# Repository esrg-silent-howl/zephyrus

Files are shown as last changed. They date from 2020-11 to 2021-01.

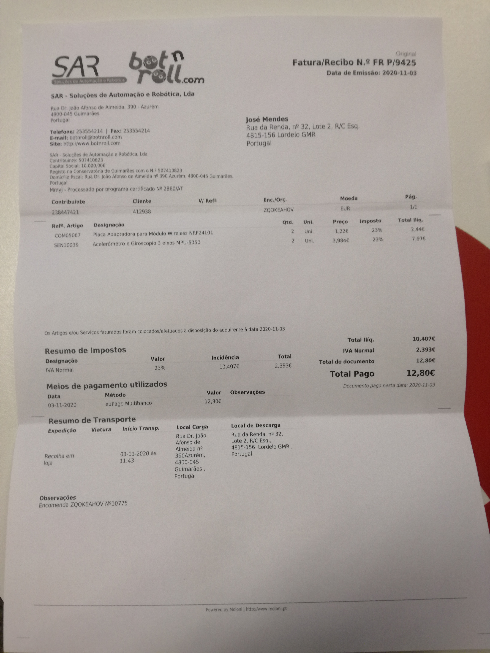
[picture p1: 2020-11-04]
Documents/Material/media/2020_11_03.jpg

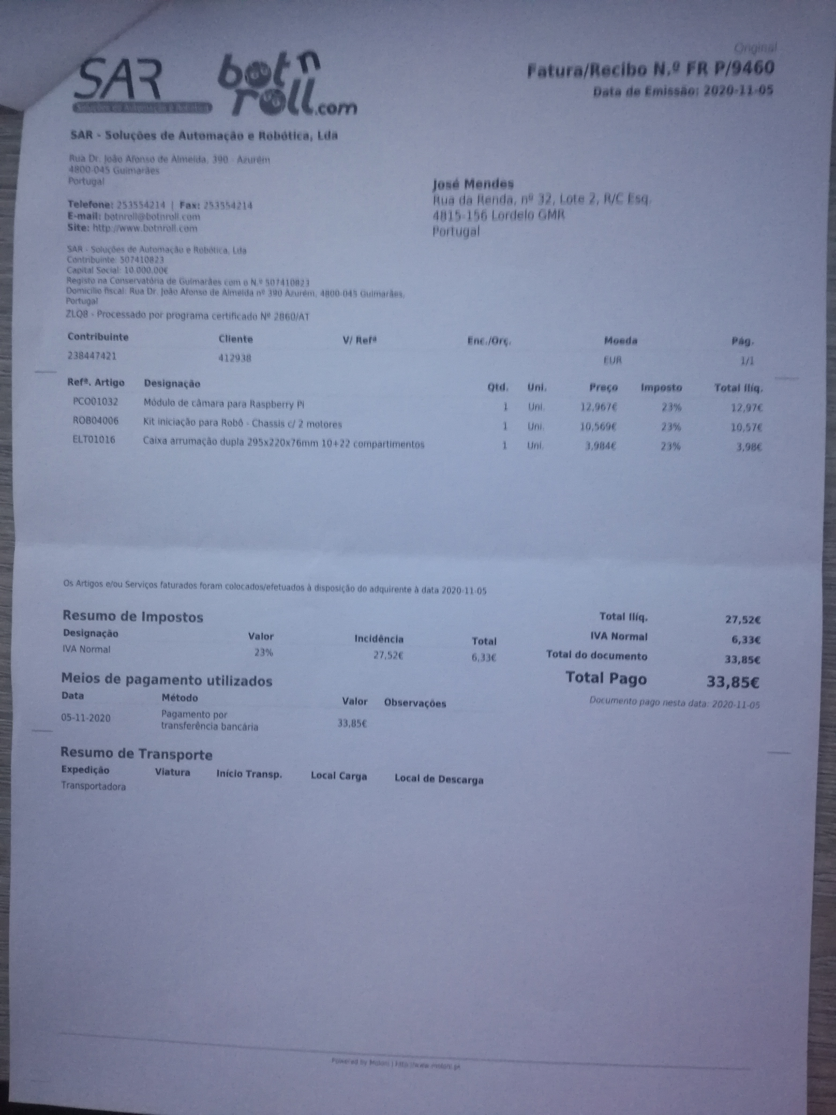
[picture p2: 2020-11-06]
Documents/Material/media/2020_11_05.jpg

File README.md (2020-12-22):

# Zephyrus
## Hand Motion-Controlled Remote Car

### Problem Statement
Recent developments in research of motion-tracking and gesture-controlled robotic
products have shone a new light on entertainment, special needs teaching, and
accessibility-focused applications. Products like motion-sensing console controllers,
robotic arms, and prosthetics have popularized and extended the knowledge on gesture
and impulse-based technologies throughout the past few years, and their market
is predicted to continue to grow in the future.
To provide a better understanding of the concepts associated with the forementioned
technologies through Research and Development (R&D), the project will consist of a
gesture-controlled car with a wristband as a remote controller. The user will be able to
accelerate and steer the vehicle using natural wrist and finger movements.

Team:
- Hugo Carvalho @HugoDaniel99
- José Mendes @h0wl-14

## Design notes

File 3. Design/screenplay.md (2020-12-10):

### **1.Introduction**

Good afternoon. We are group 7 and we are going to present the design for project 1. Its name is Zephyrus and its intent is to implement a wrist motion-controlled remote car.

### **2. Agenda**

Here is the agenda for the presentation.

- Problem Statement  
- System Overview
- Hardware and Software Architectures
- Hardware Specification
- Peripheral Interface
- Software Specification
  - Local System
  - Reinforcement Learning
  - Remote System
- Test Cases
  - Local System
  - Remote System
  - Integration
- Gantt Diagram  

### **3. Problem statement**

Motion-tracking and gesture-controlled robotics have been gaining popularity in various professional areas.  

With that in mind, this project intends to serve as a research and development tool for wearable-controlled technologies and will consist of a car, remotely controlled by a wristband using natural wrist and finger movements.  

### **4, 5, 6. System Overview**

This Figure depicts the system overview, where one can identify the main and remote boards and the ways in which they interact with each other and the external environment.

### **7. Hardware Architecture**

The Hardware for the  Local System includes: 

- A more capable main controller;
- Sensors for measuring proximity to close objects and positioning in the horizontal plane;
- Actuators for motor control ;
- A short-range wireless communications device;
- A power supply unit.

The Hardware for the Remote System includes: 

- An energy-efficient main controller;
- Sensors for measuring hand positioning;
- The counterpart for the short-range wireless communications device in the local system;
- A power supply unit.

### **8. Software Architecture**

The software architecture for both devices include high abstraction for communicating with each other and sensing modules, as well as power management and task scheduling. The local system, specifically, includes two high-level layers of abstraction for the Reinforcement Learning model.  

### **9. Hardware Specification: Local (Logic Elements)**

The main functional roles of the Local System are played by:

- A NUCLEO-F767ZI board, which hosts the main controller and all the components used to program it and make it work;
- A module containing an accelerometer/gyroscope IC that can be controlled through an I2C interface;
- A module containing a short-range radio IC and antenna instrumentation, for wireless communication;
- An board which contains an ultrasonic sensor and respective instrumentation;
- A very simple voltage level converter board to serve as **glue logic** between the main controller and the ultrasonic sensor board;
- A module containing a dual-motor driver IC.

### **10. Hardware Specification: Local (Power Supply)**

The elements that make up the power supply unit for the Local System are:

- A pair of Li-Ion batteries;
- A Battery Management System board;
- A 5V switching DC-DC step-down converter board.

### **11. Hardware Specification: Remote**

The hardware on the Remote System is comprised mainly by:

- An accelerometer and gyroscope module like the one on the Local System;
- An RF communication module that matches the one on the Local System;
- An exchangeable coin cell that serves as the main power supply for the system;
- A push button ON/OFF controller IC.

### **12. Hardware Specification: Custom Hardware (Prototype Alpha) SCH**

In order to develop for the remote system's microcontroller, a simple board was devised. This solution contains the minimum components and interfaces to be used by any microcontroller in the STM32F0 family of devices (with a QFP32 package). Additionally, it is simple enough to provide accurate real-world power profiling, necessary for alpha testing low-power applications, which is the case in this project.

The schematic for this board, designed in EAGLE CAD is represented in this image.

### **13. Hardware Specification: Custom Hardware (Prototype Alpha) BRD**

Here one can see the blueprints for that same board, with its dimensions and a glimpse of the outcome.

### **14. Hardware Specification: Custom Hardware (Prototype Beta) UC**

Following the alpha prototype, it was decided that there would be a beta prototype, containing all the integrated solutions that make up the wristband, into a slim and portable format.

With the aid of STM32CubeMX, one was able to plan out the pinout configuration and labelling for the Remote System's MCU.

### **15, 16. Hardware Specification: Custom Hardware (Prototype Beta) SCH**

Here are the initial schematics for the final wristband prototype, considering the predefined labels and separated by function into Main Logic and Power and Radio.  

### **17. Peripheral Interface: Common**

Here are the schematics documenting the interfaces between the microcontroller and the rest of the hardware. This one is for the hardware that is common to both systems...

### **18. Peripheral Interface: Specific**

... and this one is for hardware that is specific to one of the two.

### **19. Software Specification: Task Priority**

The thread pool for each system is represented in these diagrams, along with their relative priorities, statically defined. 

### **20. Software Specification: Task Timelines**

To ensure the meeting of critical timing constraints, a priority-based scheduling scheme with preemption was devised for each system. For both of them, one considered each task's worst case scenario in terms of processor time usage, as well as the power/efficiency trade-off. Dead time between task execution will be used to put the system asleep, favouring low power consumption.

### **21. Software Specification: Task Communication**

This is a diagram describing the means by which the tasks in each system interact with each other. These mechanisms satisfy what was laid out in the task timelines referring to inter-thread communication and synchronism.

### **22, 23, 24, 25. Software Specification: Threads**

As every other aspect of the project, the tasks' workflows also need a design stage. Here we can see the flowcharts for the most complex ones:

- The Local System's:
  - Gyroscope and accelerometer management task
  - RF communications management task
  - The inference task
- The Remote System's:
  - Gyroscope and accelerometer management task
  - RF communications management task

### **26. System Overview (Reinforcement Learning)**

The Local System will have a Reinforcement Learning module that is highlighted in this system overview.

### **27. System Overview (Reinforcement Learning)**

Zephyrus will rely on a feed-forward neural network that takes as input percentage speed and steer reference values, front and back measurements of distance to the nearest obstacle, and the environment state provided by the on-board sensors. With that in mind, the network will output the average percentage of the maximum voltage to be output to the motors. Percentage values were used to allow for portability to loads that require different working voltages.

### **28, 29. Test Cases**

At this stage, it is important to define a test strategy. Considering this, the tests were split into unit and integration tests taking into account alpha and beta prototypes.

### **30. Gantt Diagram**

The Gantt Diagram is presented in this slide and presents the tasks assigned to each week until the deadline.

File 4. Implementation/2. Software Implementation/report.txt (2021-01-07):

- microcontroller will shut the system off in 2 different situations:
	- user request, peacefully
	- undetermined hard fault

- check memory footprint

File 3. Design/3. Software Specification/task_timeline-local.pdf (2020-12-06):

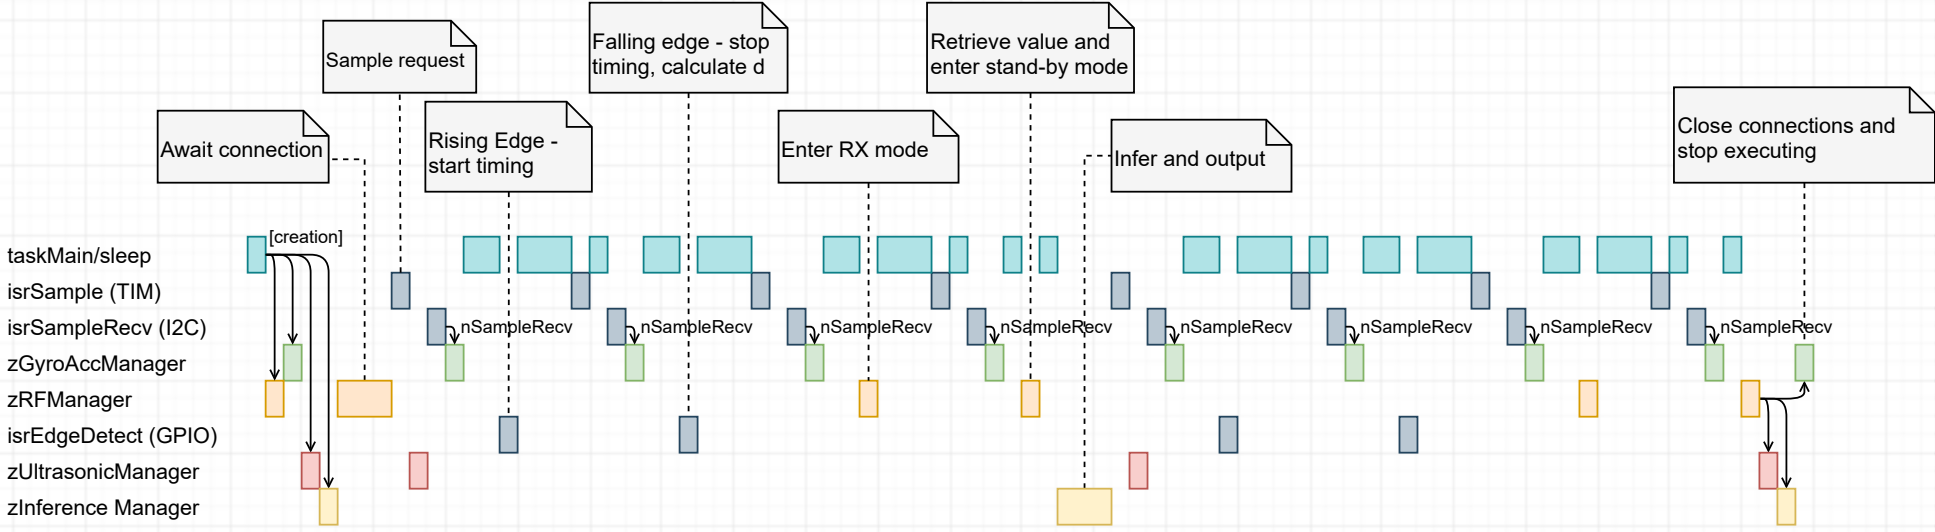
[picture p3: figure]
taskMain/sleep; isrSample (TIM); zGyroAccManager; isrSampleRecv (I2C); nSampleRecv; zRFManager; Sample request; Close connections and stop executing; [creation]; zUltrasonicManager; Enter RX mode; Retrieve value and enter stand-by mode; isrEdgeDetect (GPIO); Rising Edge - start timing; zInference Manager; Await connection; Falling edge - stop timing, calculate d; Infer and output

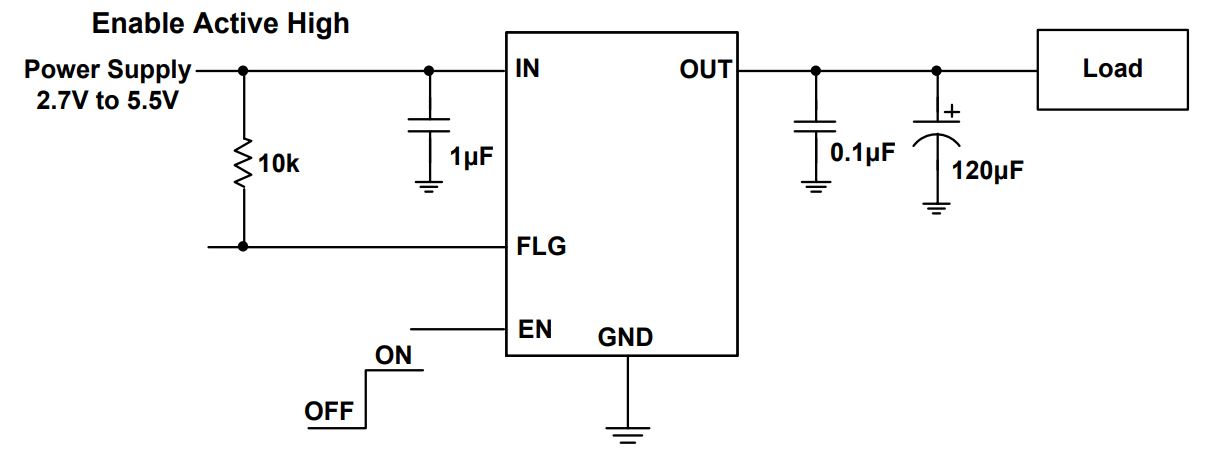
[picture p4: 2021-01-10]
3. Design/1. Hardware Specification/media/application_diagrams/ap22814.JPG

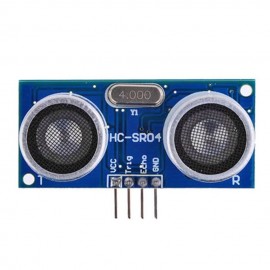
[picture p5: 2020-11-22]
3. Design/1. Hardware Specification/media/hc-sr04.jpg

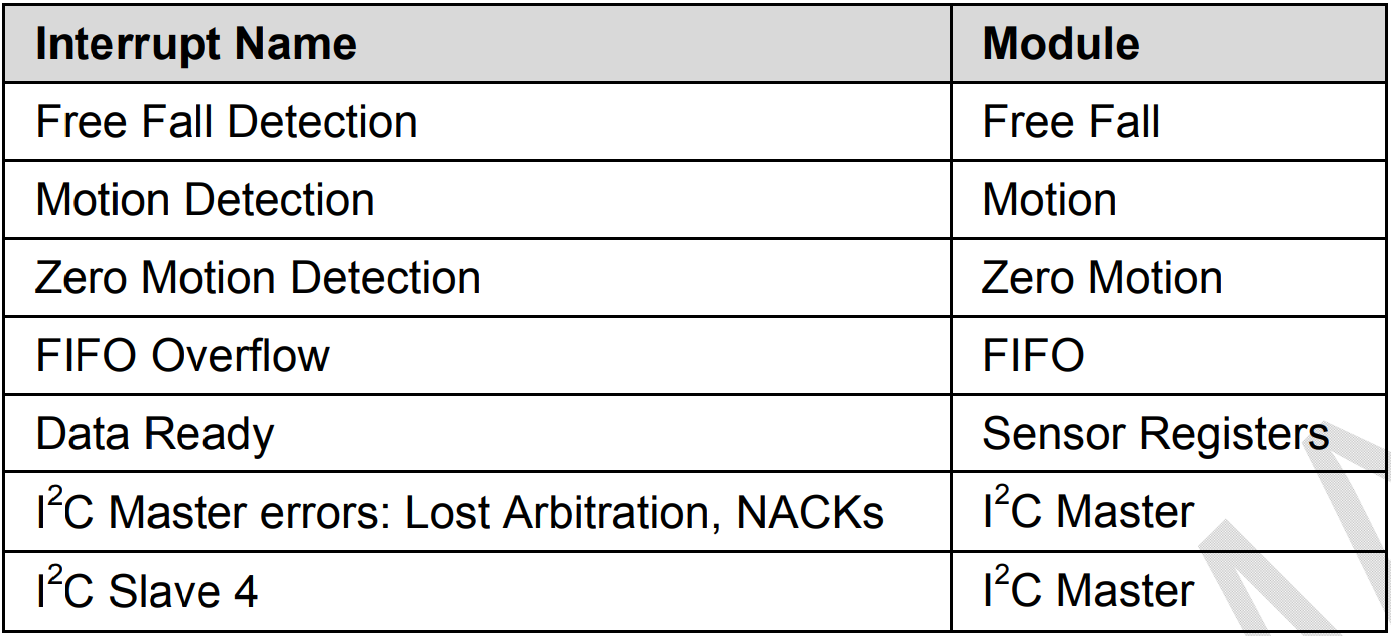
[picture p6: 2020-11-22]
3. Design/3. Software Specification/media/mpu-6050-interrupt-table.png

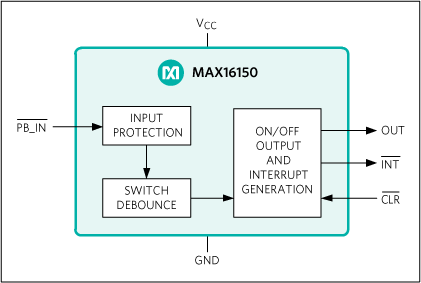
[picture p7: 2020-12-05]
3. Design/2. Interfaces/1. Peripherals/media/max16150-pinout.png

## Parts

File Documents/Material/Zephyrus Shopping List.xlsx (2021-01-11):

Date | Product Description | Quantity | Total | Store | Shipping & Customs | Element
2020-11-03 | nRF24L01+ module adapter | 2 | 3 | bot'n'roll | 0 | -
 | MPU-6050 (acc./gyro) | 2 | 9.8
2020-11-05 | Robot platform | 1 | 13 | bot'n'roll | 0 | -
2020-11-23 | STM32F051 dev board PCB | 1 | 2.11 | JLCPCB | 14.15 | -
2020-12-03 | last integrated modules | - | 32.75 | bot'n'roll | 0 | -
2020-12-22 | Wristband & PB ON/OFF PCB | - | 6.54 | JLCPCB | 12.09 | -
2020-12-22 | Components for final prototypes | - | 66.75 | Mouser | 0 | -
2020-12-29 | nRF24L01+ and nRF24L01+ module adapter | 2 | 10 | bot'n'roll | 0 | -

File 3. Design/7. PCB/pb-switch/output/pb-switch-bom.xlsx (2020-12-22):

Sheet: Sheet1
Exported
Qty | Value | Device | Package | Parts | Description | Column1 | _1
1 |  | CONN_06SILK_FEMALE_PTH | 1X06 | J2 | Multi connection point. Often used as Generic Header-pin footprint for 0.1 inch spaced/style header connections
3 | 1.4K[0603] | R-US_CHIP-0603(1608-METRIC) | RESC1608X60 | R1, R5, R6 | Resistor Fixed - ANSI
2 | 100n [0603] | C_CHIP-0603(1608-METRIC) | CAPC1608X85 | C1, C2 | Capacitor - Generic
1 | AP22814AW5-7 | AP22814AW5-7 | SOT95P285X130-5N | PS1 | DiodesZetex AP22814AW5-7, USB Power Switch, High Side, 65m, 1.6 V min. 5-Pin, SOT25
1 | B3F-1000 | B3F-1000 | B3F-1000 | SW1 | Tactile Switch SPST-NO Top Actuated Through Hole
1 | MAX16150AUT+T | MAX16150AUT+T | SOT95P280X145-6N | PB_CTRL | Supervisory Circuits Nano-Power Pushbutton ON/OFF Controller with 15kV ESD Protection and Programmable Timer
Final
Qty | Value | Device | Package | Parts | Description | Column1 | _1
3 | 1.5 KOhm | Resistor | RES0603 | R1, R5, R6 | Resistor Fixed - ANSI
2 | 100 nF | Capacitor | CAP0603 | C1, C2 | Capacitor - Generic
1 | - | AP22814AW5-7 | SOT23-5 | PS1 | High Side Power Switch
1 | - | MAX16150AUT+T | SOT23-6 | PB_CTRL | Pushbutton ON/OFF Controller

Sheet: pb_switch_bom
Qty;"Value";"Device";"Package";"Parts";"Description";"";
1;"";"CONN_06SILK_FEMALE_PTH";"1X06";"J2";"Multi connection point. Often used as Generic Header-pin footprint for 0.1 inch spaced/style header connections";"";
3;"1.4K[0603]";"R-US_CHIP-0603(1608-METRIC)";"RESC1608X60";"R1 | R5 | R6";"Resistor Fixed - ANSI";"";
2;"100n [0603]";"C_CHIP-0603(1608-METRIC)";"CAPC1608X85";"C1 | C2";"Capacitor - Generic";"";
1;"AP22814AW5-7";"AP22814AW5-7";"SOT95P285X130-5N";"PS1";"DiodesZetex AP22814AW5-7 | USB Power Switch | High Side | 65m | 1.6 V min. 5-Pin | SOT25";"";
1;"B3F-1000";"B3F-1000";"B3F-1000";"SW1";"Tactile Switch SPST-NO Top Actuated Through Hole";"";
1;"MAX16150AUT+T";"MAX16150AUT+T";"SOT95P280X145-6N";"PB_CTRL";"Supervisory Circuits Nano-Power Pushbutton ON/OFF Controller with 15kV ESD Protection and Programmable Timer";"";

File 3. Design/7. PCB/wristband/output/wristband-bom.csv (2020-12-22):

Qty | Value | Device | Package | Parts | Description | Column1 | _1
3 | 1.4K[0603] | R-US_CHIP-0603(1608-METRIC) | RESC1608X60 | R1, R5, R6 | Resistor Fixed - ANSI
2 | 1.5k [0603] | R-US_CHIP-0603(1608-METRIC) | RESC1608X60 | R3, R8 | Resistor Fixed - ANSI
2 | 100n [0603] | C_CHIP-0603(1608-METRIC) | CAPC1608X85 | C1, C2 | Capacitor - Generic
1 | 10K[0603] | R-US_CHIP-0603(1608-METRIC) | RESC1608X60 | R7 | Resistor Fixed - ANSI
5 | 10nF [0603] | CAPACITOR_0603_L | RESC0603_L | C5, C7, C21, C22, C24 | Generic chip capacitor
2 | 1nF [0603] | CAPACITOR_0603_L | RESC0603_L | C4, C6 | Generic chip capacitor
1 | 1uF [0603] | CAPACITOR_0603_L | RESC0603_L | C23 | Generic chip capacitor
1 | 2.2 nF [0603] | CAPACITOR_0603_L | RESC0603_L | C8 | Generic chip capacitor
1 | 22K[0603] | R-US_CHIP-0603(1608-METRIC) | RESC1608X60 | R2 | Resistor Fixed - ANSI
5 | 22nF [1206] | CL31B226KPHNNNE | CAPC3216X180N | C10, C11, C12, C13, C14 | 22F +/-10% 10V Ceramic Capacitor X7R 1206 (3216 Metric)
4 | 22pF [0603] | CAPACITOR_0603_L | RESC0603_L | C15, C16, C17, C18 | Generic chip capacitor
1 | 2450BM14A0002T | 2450BM14A0002T | 2450BM14A0002T | ANT1 | JOHANSON TECHNOLOGY - 2450BM14A0002T - BALUN, 2.45GHZ, IMPEDANCE MATCHED
1 | 33nF [0603] | CAPACITOR_0603_L | RESC0603_L | C3 | Generic chip capacitor
2 | 4.7uF [0603] | CAPACITOR_0603_L | RESC0603_L | C19, C20 | Generic chip capacitor
1 | AP22814AW5-7 | AP22814AW5-7 | SOT95P285X130-5N | PS2 | DiodesZetex AP22814AW5-7, USB Power Switch, High Side, 65m, 1.6 V min. 5-Pin, SOT25
1 | BAT-HLD-001 | BAT-HLD-001 | BATHLD001 | BATT_HLD | Coin Cell Battery Holders Linx CR2032 Battery Holder
1 | DELLS1.22-AMBER | KS_DELLS1.22-JHKI-1 | KSDELLS122JHKI1 | LEDPWR | Standard LEDs - SMD Super Red TOPLED E 1608
1 | DELLS1.22-GREEN | KS_DELLS1.22-JHKI-1 | KSDELLS122JHKI1 | LEDCONNPROB | Standard LEDs - SMD Super Red TOPLED E 1608
2 | FA-20H_16.0000MF12Z-AC3 | FA-20H_16.0000MF12Z-AC3 | FA20H160000MF12ZAC3 | Y2, Y3 | Crystals 16MHz 10ppm 9pF -20C +75C
2 | M20-7910542R | M20-7910542R | M207910542R | MPU_6050_IF, PROG_IF | Headers & Wire Housings 5 WAY SIL HORIZ SMT SKT T&R
1 | MAX16150AUT+T | MAX16150AUT+T | SOT95P280X145-6N | PB_CTRL | Supervisory Circuits Nano-Power Pushbutton ON/OFF Controller with 15kV ESD Protection and Programmable Timer
1 | MIFA-CYPRESS-2 | MIFA-CYPRESS-2 | MIFA-CYPRESS-2 | MIFA
1 | NRF24L01P-T | NRF24L01P-T | QFN50P400X400X95-21N | NRF24L01+ | RF Transceiver IC 2.4GHz ISM Band QFN20 Nordic Semiconductor NRF24L01P-T, RF Transceiver 2400MHz to 2483.5MHz 1.9 3.6 V 20-Pin QFN
1 | PTS636_SM43_SMTR_LFS | PTS636_SM43_SMTR_LFS | PTS636SM43SMTRLFS | S2 | Tactile Switches Tact 50mA 12VDC, 6.0x3.5, 4.3mm H, 180gf, G leads, No ground pin, Black Actuator
1 | STM32F051K8T6 | STM32F051K8T6 | QFP80P900X900X160-32N | IC1 | Source: Datasheet

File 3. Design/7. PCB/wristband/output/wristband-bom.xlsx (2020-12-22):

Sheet: Sheet1
Exported
Qty | Value | Device | Package | Parts | Description
3 | 1.4K[0603] | R-US_CHIP-0603(1608-METRIC) | RESC1608X60 | R1, R5, R6 | Resistor Fixed - ANSI
2 | 1.5k [0603] | R-US_CHIP-0603(1608-METRIC) | RESC1608X60 | R3, R8 | Resistor Fixed - ANSI
2 | 100n [0603] | C_CHIP-0603(1608-METRIC) | CAPC1608X85 | C1, C2 | Capacitor - Generic
1 | 10K[0603] | R-US_CHIP-0603(1608-METRIC) | RESC1608X60 | R7 | Resistor Fixed - ANSI
5 | 10nF [0603] | CAPACITOR_0603_L | RESC0603_L | C5, C7, C21, C22, C24 | Generic chip capacitor
2 | 1nF [0603] | CAPACITOR_0603_L | RESC0603_L | C4, C6 | Generic chip capacitor
1 | 1uF [0603] | CAPACITOR_0603_L | RESC0603_L | C23 | Generic chip capacitor
1 | 2.2 nF [0603] | CAPACITOR_0603_L | RESC0603_L | C8 | Generic chip capacitor
1 | 22K[0603] | R-US_CHIP-0603(1608-METRIC) | RESC1608X60 | R2 | Resistor Fixed - ANSI
5 | 22nF [1206] | CL31B226KPHNNNE | CAPC3216X180N | C10, C11, C12, C13, C14 | 22F +/-10% 10V Ceramic Capacitor X7R 1206 (3216 Metric)
4 | 22pF [0603] | CAPACITOR_0603_L | RESC0603_L | C15, C16, C17, C18 | Generic chip capacitor
1 | 2450BM14A0002T | 2450BM14A0002T | 2450BM14A0002T | ANT1 | JOHANSON TECHNOLOGY - 2450BM14A0002T - BALUN, 2.45GHZ, IMPEDANCE MATCHED
1 | 33nF [0603] | CAPACITOR_0603_L | RESC0603_L | C3 | Generic chip capacitor
2 | 4.7uF [0603] | CAPACITOR_0603_L | RESC0603_L | C19, C20 | Generic chip capacitor
1 | AP22814AW5-7 | AP22814AW5-7 | SOT95P285X130-5N | PS2 | DiodesZetex AP22814AW5-7, USB Power Switch, High Side, 65m, 1.6 V min. 5-Pin, SOT25
1 | BAT-HLD-001 | BAT-HLD-001 | BATHLD001 | BATT_HLD | Coin Cell Battery Holders Linx CR2032 Battery Holder
1 | DELLS1.22-AMBER | KS_DELLS1.22-JHKI-1 | KSDELLS122JHKI1 | LEDPWR | Standard LEDs - SMD Super Red TOPLED E 1608
1 | DELLS1.22-GREEN | KS_DELLS1.22-JHKI-1 | KSDELLS122JHKI1 | LEDCONNPROB | Standard LEDs - SMD Super Red TOPLED E 1608
2 | FA-20H_16.0000MF12Z-AC3 | FA-20H_16.0000MF12Z-AC3 | FA20H160000MF12ZAC3 | Y2, Y3 | Crystals 16MHz 10ppm 9pF -20C +75C
2 | M20-7910542R | M20-7910542R | M207910542R | MPU_6050_IF, PROG_IF | Headers & Wire Housings 5 WAY SIL HORIZ SMT SKT T&R
1 | MAX16150AUT+T | MAX16150AUT+T | SOT95P280X145-6N | PB_CTRL | Supervisory Circuits Nano-Power Pushbutton ON/OFF Controller with 15kV ESD Protection and Programmable Timer
1 | MIFA-CYPRESS-2 | MIFA-CYPRESS-2 | MIFA-CYPRESS-2 | MIFA
1 | NRF24L01P-T | NRF24L01P-T | QFN50P400X400X95-21N | NRF24L01+ | RF Transceiver IC 2.4GHz ISM Band QFN20 Nordic Semiconductor NRF24L01P-T, RF Transceiver 2400MHz to 2483.5MHz 1.9 3.6 V 20-Pin QFN
1 | PTS636_SM43_SMTR_LFS | PTS636_SM43_SMTR_LFS | PTS636SM43SMTRLFS | S2 | Tactile Switches Tact 50mA 12VDC, 6.0x3.5, 4.3mm H, 180gf, G leads, No ground pin, Black Actuator
1 | STM32F051K8T6 | STM32F051K8T6 | QFP80P900X900X160-32N | IC1 | Source: Datasheet
Final
Qty | Value | Device | Package | Parts | Description
5 | 1.5 KOhm | Resistor | RES0603 | R3, R8 | Resistor Fixed - ANSI
2 | 100 nF | Capacitor | CAP0603 | C1, C2 | Capacitor - Generic
1 | 10 KOhm | Resistor | RES0603 | R7 | Resistor Fixed - ANSI
5 | 10 nF | Capacitor | CAP0603 | C5, C7, C21, C22, C24 | Generic chip capacitor
2 | 1 nF | Capacitor | CAP0603 | C4, C6 | Generic chip capacitor
1 | 1 uF | Capacitor | CAP0603 | C23 | Generic chip capacitor
1 | 2.2 nF | Capacitor | CAP0603 | C8 | Generic chip capacitor
1 | 22 Kohm | Resistor | RES0603 | R2 | Resistor Fixed - ANSI
5 | 22 nF | Capacitor | CAP1206 | C10, C11, C12, C13, C14 | 22F +/-10% 10V Ceramic Capacitor
4 | 22 pF | Capacitor | CAP0603 [C0G] | C15, C16, C17, C18 | Generic chip capacitor
1 | - | 2450BM14A0002T | 2450BM14A0002T | ANT1 | Balun and filter, 2.45GHz
1 | 33 nF | Capacitor | CAP0603 | C3 | Generic chip capacitor
2 | 4.7 uF | Capacitor | CAP0603 | C19, C20 | Generic chip capacitor
1 | - | AP22814AW5-7 | SOT23-5 | PS1 | High Side Power Switch
1 | - | BAT-HLD-001 | BATHLD001 | BATT_HLD | Coin Cell Battery Holder
1 | - | KO DELLS1.22-KHLI-24 | LED0603 [A] | LEDPWR | Standard LEDs - SMD Amber TOPLED E 1608
1 | - | KP DELLS1.22-FGGI-25 | LED0603 [G] | LEDCONNPROB | Standard LEDs - SMD Green TOPLED E 1608
2 | - | FA-20H_16.0000MF12Z-AC3 | SG-710 (Ceramic SMD) | Y2, Y3 | Crystals 16MHz 10ppm 9pF -20C +75C
2 | - | M20-7910542R | 2.54mm | MPU_6050_IF, PROG_IF | Headers 5 WAY SIL
1 | - | MAX16150AUT+T | SOT23-6 | PB_CTRL | Pushbutton ON/OFF Controller
1 | - | NRF24L01P-T | QFN-20 | NRF24L01+ | RF Transceiver IC 2.4GHz
1 | - | PTS636_SM43_SMTR_LFS | PTS636SM43SMTRLFS | S2 | Tactile Switch
1 | - | STM32F051K6T6 | QFP-32 | IC1 | 32-bit ARM Microcontroller
Budget
Qty | Value | Device | Unit Price | 10K Unit Price | Package | Parts
5 | 1.5 KOhm | Resistor |  |  | RES0603 | R3, R8
2 | 100 nF | Capacitor |  |  | CAP0603 | C1, C2
1 | 100 KOhm | Resistor |  |  | RES0603 | R7
5 | 10 nF | Capacitor |  |  | CAP0603 | C5, C7, C21, C22, C24
2 | 1 nF | Capacitor |  |  | CAP0603 | C4, C6
1 | 1 uF | Capacitor |  |  | CAP0603 | C23
1 | 2.2 nF | Capacitor |  |  | CAP0603 | C8
1 | 22 Kohm | Resistor |  |  | RES0603 | R2
5 | 22/100 nF | Capacitor |  |  | CAP1206 | C10, C11, C12, C13, C14
4 | 22 pF | Capacitor | 0.076 | 0.008 | CAP0603 [C0G, +/- 2%] | C15, C16, C17, C18
1 | - | 2450BM14A0002T | 0.754 | 0.287 | 2450BM14A0002T | ANT1
1 | 33 nF | Capacitor |  |  | CAP0603 | C3
2 | 4.7 uF | Capacitor |  |  | CAP0603 | C19, C20
1 | - | AP22814AW5-7 | 0.407 | 0.218 | SOT23-5 | PS1
1 | - | BAT-HLD-001 | 0.246 | 0.176 | BATHLD001 | BATT_HLD
1 | - | KO DELLS1.22-KHLI-24 | 0.339 | 0.039 | LED0603 [A] | LEDPWR
1 | - | KP DELLS1.22-FGGI-25 | 0.322 | 0.059 | LED0603 [G] | LEDCONNPROB
2 | - | FA-20H_16.0000MF12Z-AC3 | 0.424 | 0.181 | SG-710 (Ceramic SMD) | Y2, Y3
1 | - | MAX16150AUT+T | 1.55 | 1.13 | SOT23-6 | PB_CTRL
1 | - | NRF24L01P-T | 2.85 | 1.33 | QFN-20 | NRF24L01+
1 | - | PTS636_SM43_SMTR_LFS | 0.102 | 0.059 | PTS636SM43SMTRLFS | S2
1 | - | STM32F051K6T6 | 2.35 | 1.04 | QFP-32 | IC1
 |  |  | 10.072 | 4.732

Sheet: wristband-bom
Qty;"Value";"Device";"Package";"Parts";"Description";"";
3;"1.4K[0603]";"R-US_CHIP-0603(1608-METRIC)";"RESC1608X60";"R1 | R5 | R6";"Resistor Fixed - ANSI";"";
2;"1.5k [0603]";"R-US_CHIP-0603(1608-METRIC)";"RESC1608X60";"R3 | R8";"Resistor Fixed - ANSI";"";
2;"100n [0603]";"C_CHIP-0603(1608-METRIC)";"CAPC1608X85";"C1 | C2";"Capacitor - Generic";"";
1;"10K[0603]";"R-US_CHIP-0603(1608-METRIC)";"RESC1608X60";"R7";"Resistor Fixed - ANSI";"";
5;"10nF [0603]";"CAPACITOR_0603_L";"RESC0603_L";"C5 | C7 | C21 | C22 | C24";"Generic chip capacitor";"";
2;"1nF [0603]";"CAPACITOR_0603_L";"RESC0603_L";"C4 | C6";"Generic chip capacitor";"";
1;"1uF [0603]";"CAPACITOR_0603_L";"RESC0603_L";"C23";"Generic chip capacitor";"";
1;"2.2 nF [0603]";"CAPACITOR_0603_L";"RESC0603_L";"C8";"Generic chip capacitor";"";
1;"22K[0603]";"R-US_CHIP-0603(1608-METRIC)";"RESC1608X60";"R2";"Resistor Fixed - ANSI";"";
5;"22nF [1206]";"CL31B226KPHNNNE";"CAPC3216X180N";"C10 | C11 | C12 | C13 | C14";"22F +/-10% 10V Ceramic Capacitor X7R 1206 (3216 Metric)";"";
4;"22pF [0603]";"CAPACITOR_0603_L";"RESC0603_L";"C15 | C16 | C17 | C18";"Generic chip capacitor";"";
1;"2450BM14A0002T";"2450BM14A0002T";"2450BM14A0002T";"ANT1";"JOHANSON TECHNOLOGY - 2450BM14A0002T - BALUN | 2.45GHZ | IMPEDANCE MATCHED";"";
1;"33nF [0603]";"CAPACITOR_0603_L";"RESC0603_L";"C3";"Generic chip capacitor";"";
2;"4.7uF [0603]";"CAPACITOR_0603_L";"RESC0603_L";"C19 | C20";"Generic chip capacitor";"";
1;"AP22814AW5-7";"AP22814AW5-7";"SOT95P285X130-5N";"PS2";"DiodesZetex AP22814AW5-7 | USB Power Switch | High Side | 65m | 1.6 V min. 5-Pin | SOT25";"";
1;"BAT-HLD-001";"BAT-HLD-001";"BATHLD001";"BATT_HLD";"Coin Cell Battery Holders Linx CR2032 Battery Holder";"";
1;"DELLS1.22-AMBER";"KS_DELLS1.22-JHKI-1";"KSDELLS122JHKI1";"LEDPWR";"Standard LEDs - SMD Super Red TOPLED E 1608";"";
1;"DELLS1.22-GREEN";"KS_DELLS1.22-JHKI-1";"KSDELLS122JHKI1";"LEDCONNPROB";"Standard LEDs - SMD Super Red TOPLED E 1608";"";
2;"FA-20H_16.0000MF12Z-AC3";"FA-20H_16.0000MF12Z-AC3";"FA20H160000MF12ZAC3";"Y2 | Y3";"Crystals 16MHz 10ppm 9pF -20C +75C";"";
2;"M20-7910542R";"M20-7910542R";"M207910542R";"MPU_6050_IF | PROG_IF";"Headers & Wire Housings 5 WAY SIL HORIZ SMT SKT T&R";"";
1;"MAX16150AUT+T";"MAX16150AUT+T";"SOT95P280X145-6N";"PB_CTRL";"Supervisory Circuits Nano-Power Pushbutton ON/OFF Controller with 15kV ESD Protection and Programmable Timer";"";
1;"MIFA-CYPRESS-2";"MIFA-CYPRESS-2";"MIFA-CYPRESS-2";"MIFA";"";"";
1;"NRF24L01P-T";"NRF24L01P-T";"QFN50P400X400X95-21N";"NRF24L01+";"RF Transceiver IC 2.4GHz ISM Band QFN20 Nordic Semiconductor NRF24L01P-T | RF Transceiver 2400MHz to 2483.5MHz 1.9 3.6 V 20-Pin QFN";"";
1;"PTS636_SM43_SMTR_LFS";"PTS636_SM43_SMTR_LFS";"PTS636SM43SMTRLFS";"S2";"Tactile Switches Tact 50mA 12VDC | 6.0x3.5 | 4.3mm H | 180gf | G leads | No ground pin | Black Actuator";"";
1;"STM32F051K8T6";"STM32F051K8T6";"QFP80P900X900X160-32N";"IC1";"Source: Datasheet";"";

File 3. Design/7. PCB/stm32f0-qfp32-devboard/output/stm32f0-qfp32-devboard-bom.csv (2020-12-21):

Qty | Value | Device | Package | Parts | Description
2 |  | CONN_02 | 1X02 | J4, J5 | Multi connection point. Often used as Generic Header-pin footprint for 0.1 inch spaced/style header connections
1 |  | CONN_05 | 1X05 | J3 | Multi connection point. Often used as Generic Header-pin footprint for 0.1 inch spaced/style header connections
2 |  | CONN_13 | 1X13 | J1, J2 | Multi connection point. Often used as Generic Header-pin footprint for 0.1 inch spaced/style header connections
2 | 100n | C2012X7R1H104K085AA | CAPC2012X100N | C1, C2 | TDK C2012 C 100nF Ceramic Multilayer Capacitor, 50 V dc, +125C, X7R Dielectric, +/-10% SMD
2 | 10u | C3216X7R1C106K160AC | CAPC3216X180N | C3, C4 | 1206 X7R ceramic capacitor 16V 10uF TDK C3216 C 10uF Ceramic Multilayer Capacitor, 16 V dc X7R Dielectric +/-10% SMD
1 | 110k | 0.22OHM-0805-1/4W-1% | 0805 | R1 | 0.22Ω resistor
1 | STM32F051 | STM32F051K8T6 | QFP80P900X900X160-32N | IC1 | Source: Datasheet

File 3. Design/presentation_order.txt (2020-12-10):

H 1
H 2
Z 3
Z 4,5,6
Z 7
H 8
H 9
Z 10
Z 11
H 12
H 13
Z 14
Z 15,16
H 17
H 18
Z 19
Z 20
Z 21
H 22,23,24,25
H 26
H 27
Z 28,29
Z 30

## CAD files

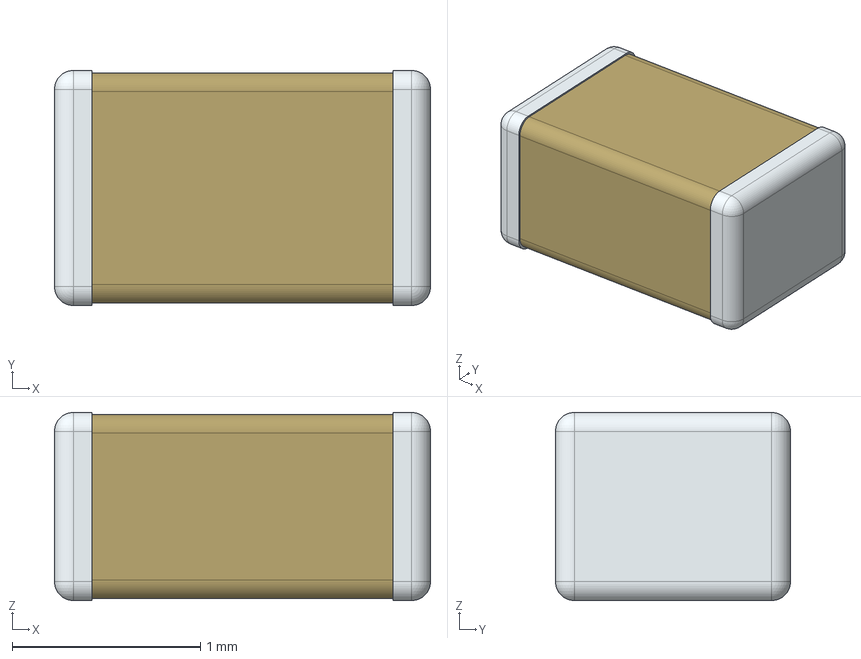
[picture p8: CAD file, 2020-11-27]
3. Design/7. PCB/stm32f0-qfp32-devboard/models/3D/C2012X7R1H104K085AA.stp
2.00 x 1.25 x 1.00 mm

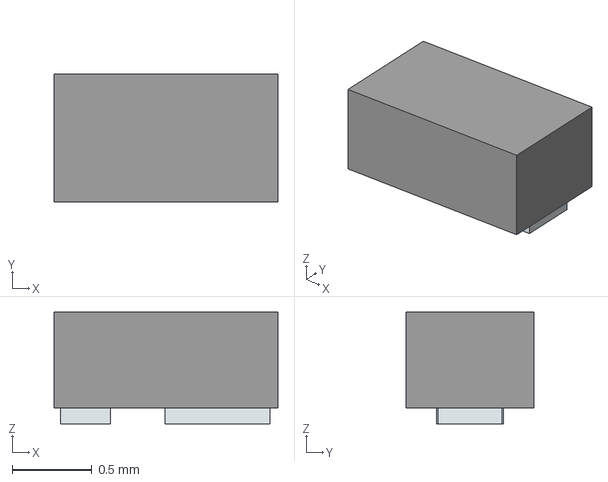
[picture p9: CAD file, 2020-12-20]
3. Design/7. PCB/wristband/model/parts/stp/CH_DELSS1.22-S1T2-35.stp
1.40 x 0.8 x 0.7 mm
Pins

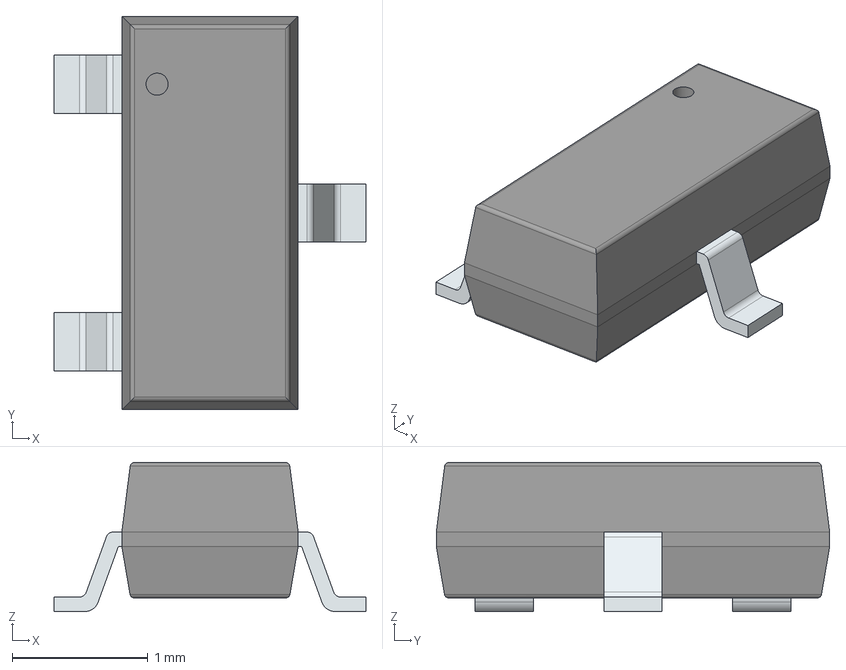
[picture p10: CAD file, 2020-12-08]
3. Design/7. PCB/pb-switch/model/parts/stp/2N7002NXAKR.stp
2.30 x 2.90 x 1.10 mm
PinsArrayL
FilletPinR

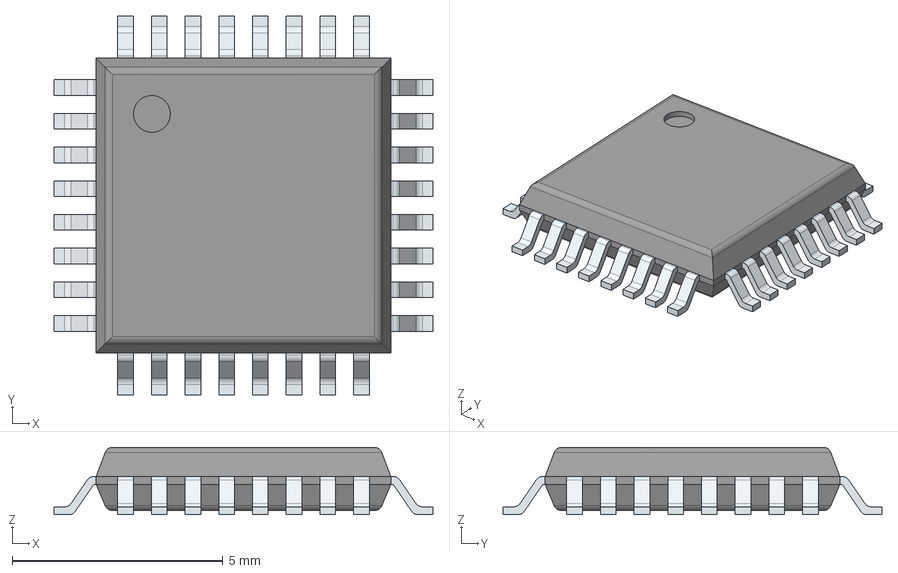
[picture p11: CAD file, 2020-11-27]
3. Design/7. PCB/stm32f0-qfp32-devboard/models/3D/STM32F051K6T6.stp
9.00 x 9.00 x 1.60 mm
PinsArrayLR
PinsArrayTB

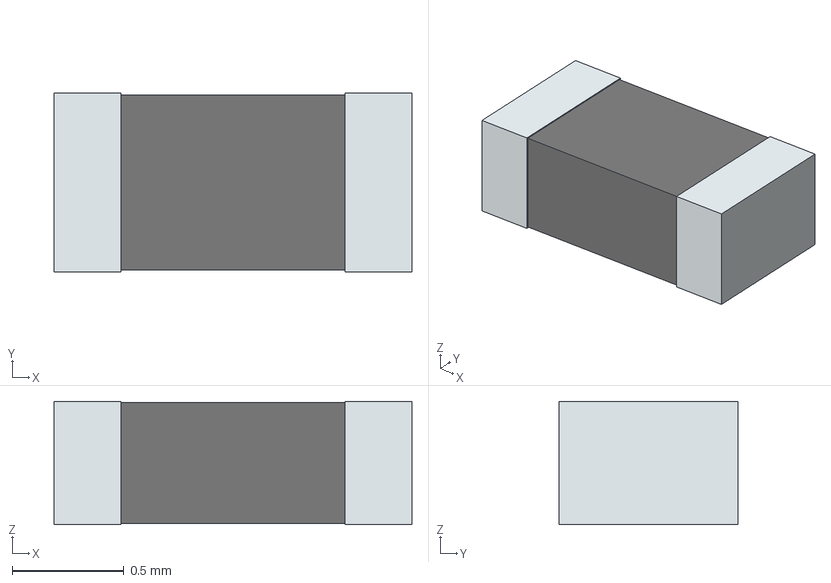
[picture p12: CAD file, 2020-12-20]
3. Design/7. PCB/wristband/model/parts/stp/res_0603.stp
1.60 x 0.8 x 0.55 mm
term1
term2

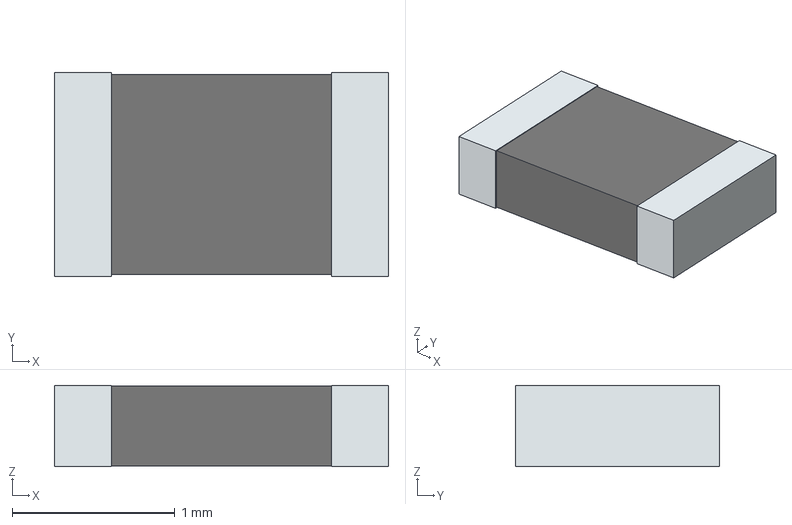
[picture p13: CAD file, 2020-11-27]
3. Design/7. PCB/stm32f0-qfp32-devboard/models/3D/CRCW0805100KFKEA.stp
2.05 x 1.25 x 0.5 mm
term1
term2

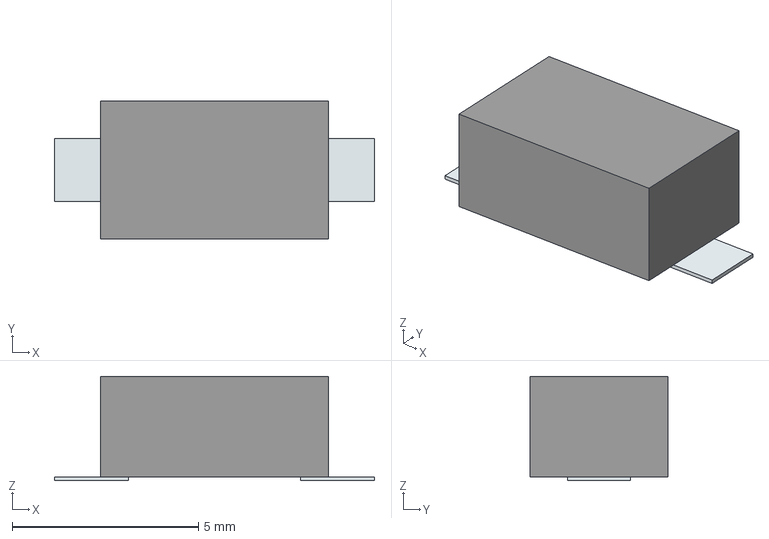
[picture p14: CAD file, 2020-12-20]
3. Design/7. PCB/wristband/model/parts/stp/PTS636_SM25F_SMTR_LFS.stp
8.58 x 3.70 x 2.80 mm
Pins

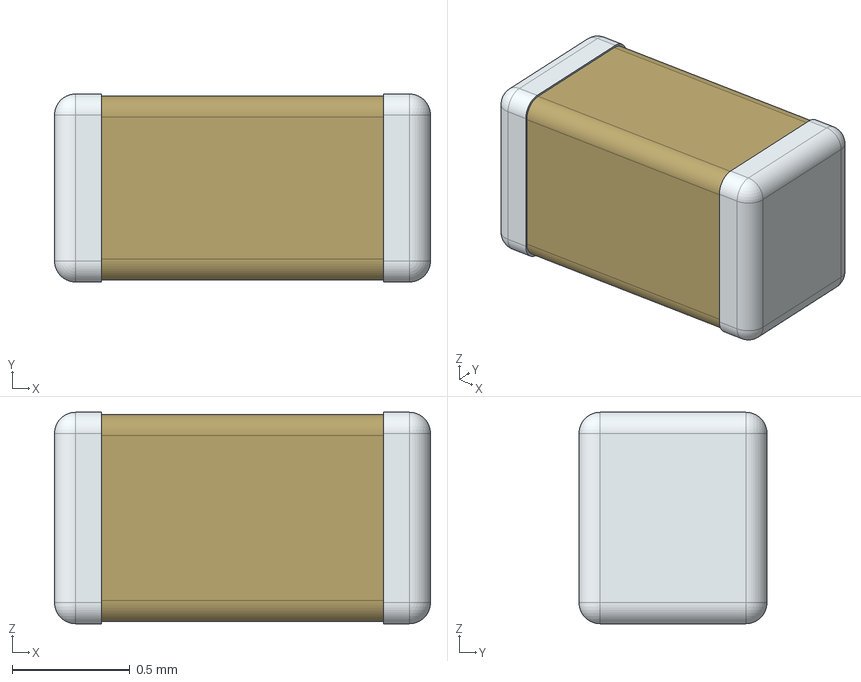
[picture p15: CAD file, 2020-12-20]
3. Design/7. PCB/wristband/model/parts/stp/cap_0603.stp
1.60 x 0.8 x 0.9 mm

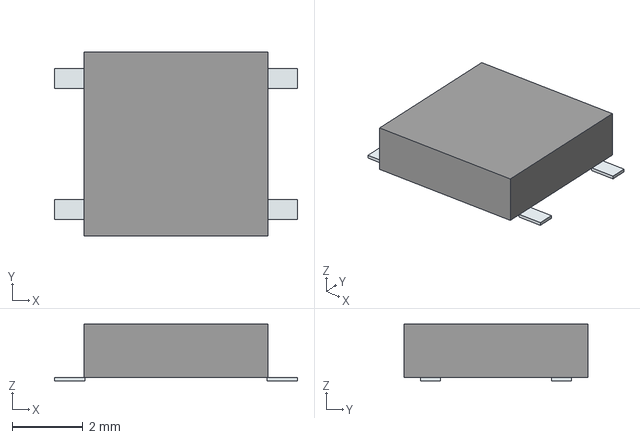
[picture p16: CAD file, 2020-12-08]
3. Design/7. PCB/wristband/model/parts/stp/PTS526_SM15_SMTR2_LFS.stp
6.86 x 5.20 x 1.60 mm
Pins

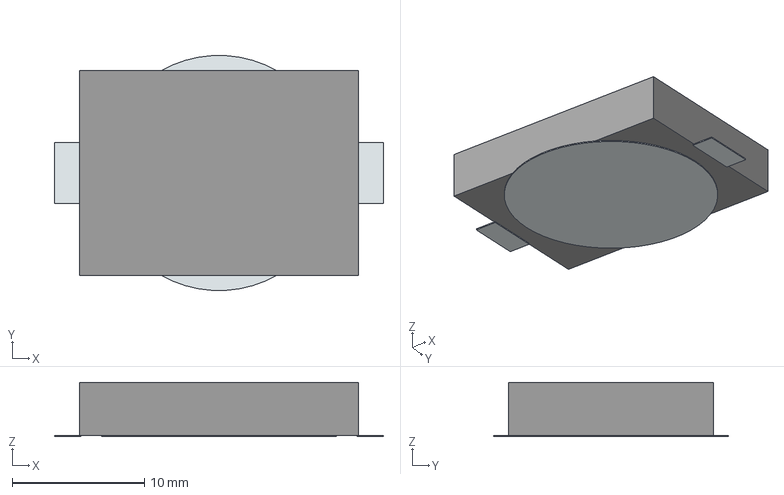
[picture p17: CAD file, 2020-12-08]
3. Design/7. PCB/wristband/model/parts/stp/BAT-HLD-001.stp
24.9 x 17.8 x 4.10 mm
Pins

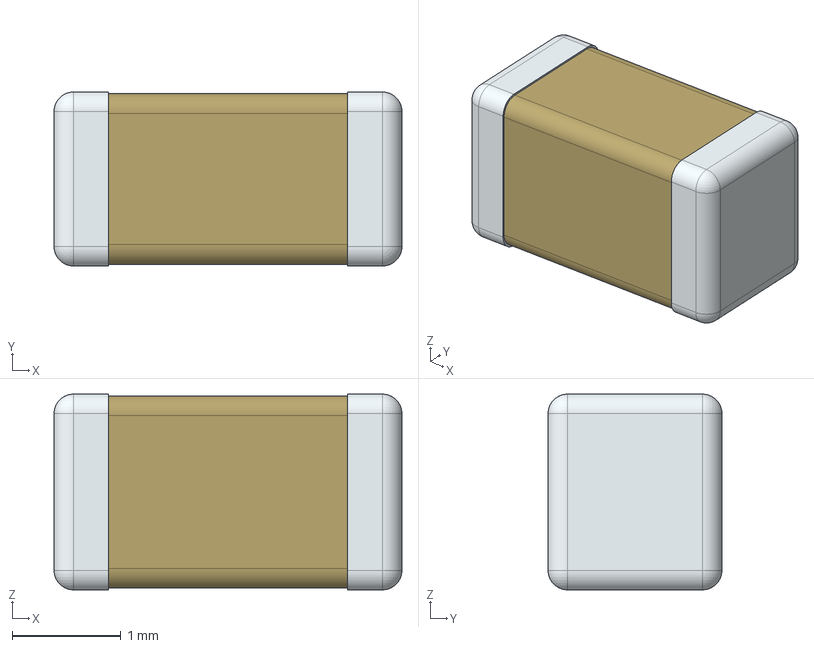
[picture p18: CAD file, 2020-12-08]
3. Design/7. PCB/wristband/model/parts/stp/CL31B226KPHNNNE.stp
3.20 x 1.60 x 1.80 mm

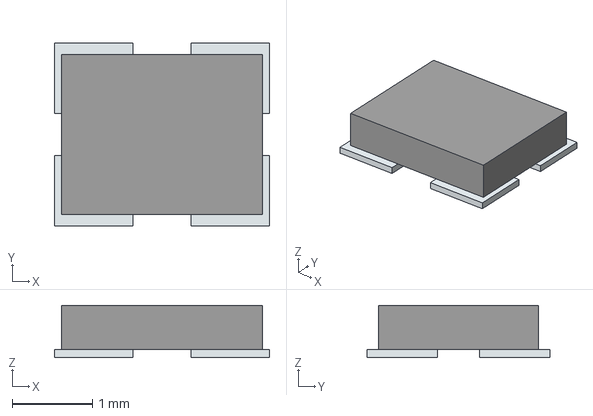
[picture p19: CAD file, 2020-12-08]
3. Design/7. PCB/wristband/model/parts/stp/FA-20H_16.0000MF12Z-AC3.stp
2.68 x 2.28 x 0.65 mm
Pins

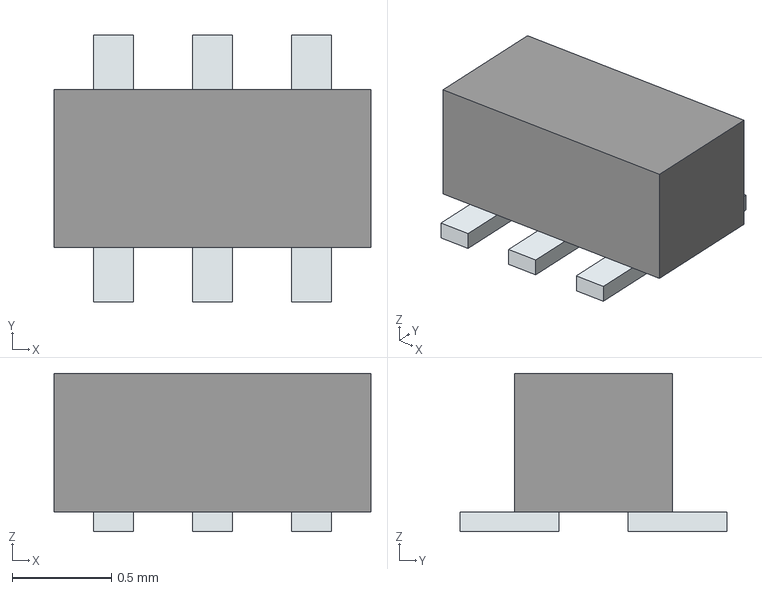
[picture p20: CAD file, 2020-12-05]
3. Design/7. PCB/wristband/model/parts/stp/2450BM14A0002T.stp
1.60 x 1.35 x 0.8 mm
Pins

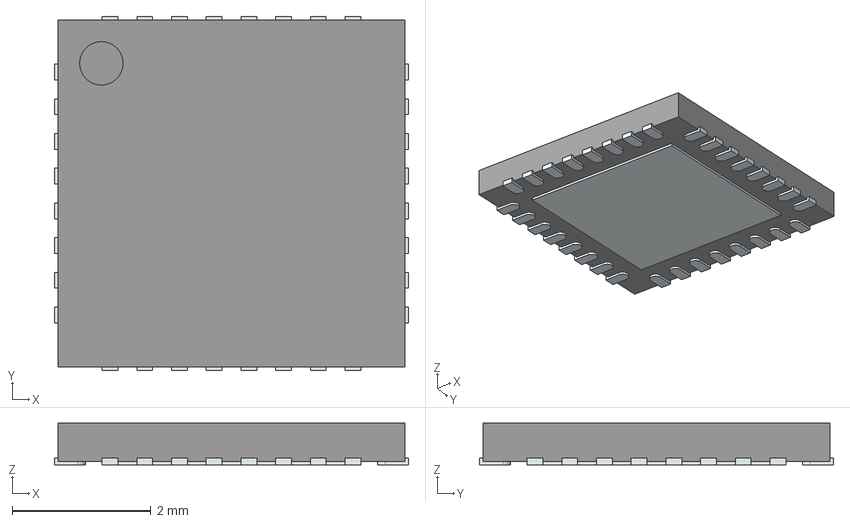
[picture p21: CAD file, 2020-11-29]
3. Design/7. PCB/wristband/model/parts/stp/STM32F051K6U6.stp
5.10 x 5.10 x 0.6 mm
ThermalPin
PinsArrayLR
PinsArrayTB

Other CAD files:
3. Design/7. PCB/wristband/model/parts/stp/nRF24L01P-T.stp
3. Design/7. PCB/wristband/model/parts/stp/MPU-6050.stp
3. Design/7. PCB/wristband/model/parts/stp/cap_1206.stp
3. Design/7. PCB/pb-switch/model/parts/stp/AP22814AW5-7.stp
3. Design/7. PCB/pb-switch/model/parts/stp/MAX16150AUT+T.stp
3. Design/7. PCB/pb-switch/output/3d/pb-switch-pcb.f3d
3. Design/7. PCB/stm32f0-qfp32-devboard/output/3d/stm32f0-qfp32-devboard.f3d
3. Design/7. PCB/wristband/output/3d/wristband.f3d

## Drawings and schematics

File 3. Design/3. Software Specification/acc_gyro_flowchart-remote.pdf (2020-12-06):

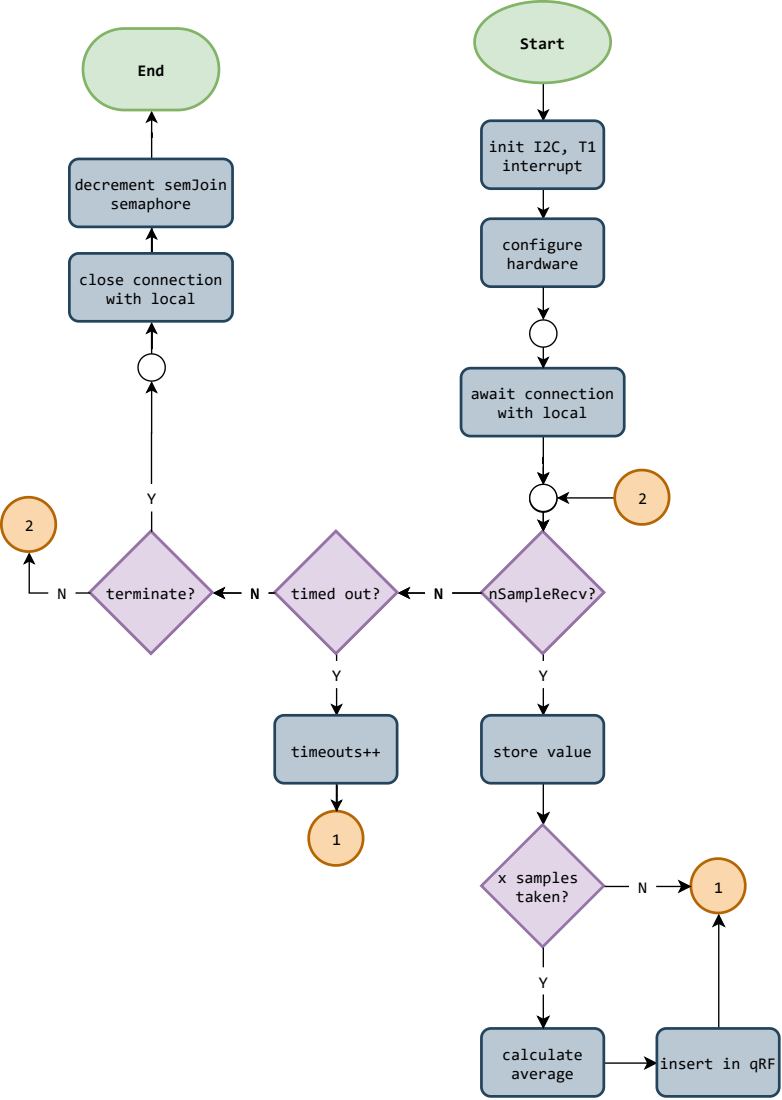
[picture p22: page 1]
data; terminate?; timeouts++; store value; calculate average; x samples taken?; timed out?; nSampleRecv?; Start; init I2C, T1 interrupt; configure hardware; await connection with local; close connection with local; decrement semJoin semaphore; End

received? timed out?

insert in qRF

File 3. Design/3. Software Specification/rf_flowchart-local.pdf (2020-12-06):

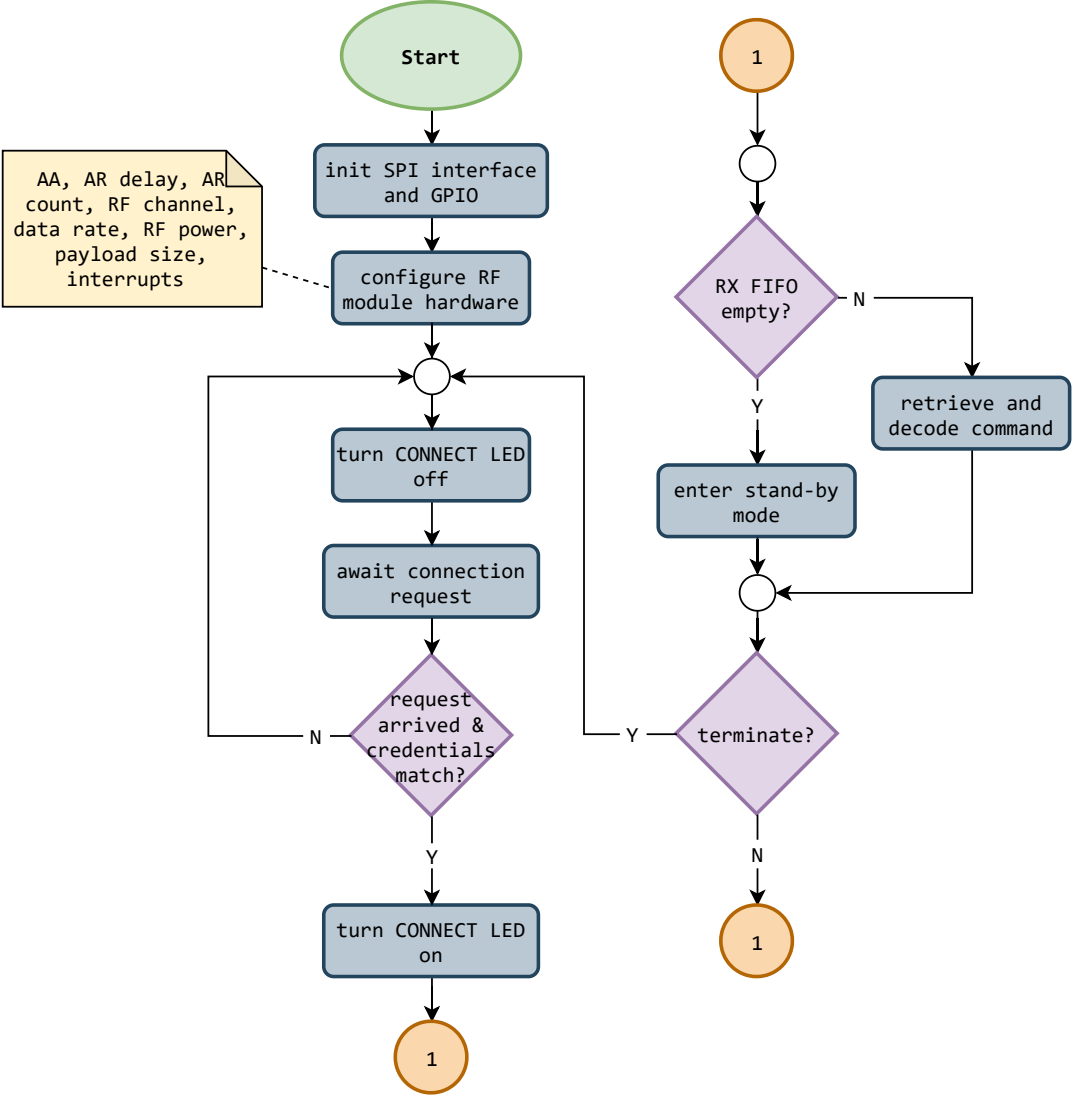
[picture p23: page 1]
Start; configure RF module hardware; await; connection; request; arrived; credentials match?; RX FIFO empty?; terminate?; off; retrieve and decode command

AA, AR delay, AR
count, RF channel,
data rate, RF power,
payload size,
interrupts

init SPI interface
and GPIO

turn CONNECT LED

enter stand-by
mode

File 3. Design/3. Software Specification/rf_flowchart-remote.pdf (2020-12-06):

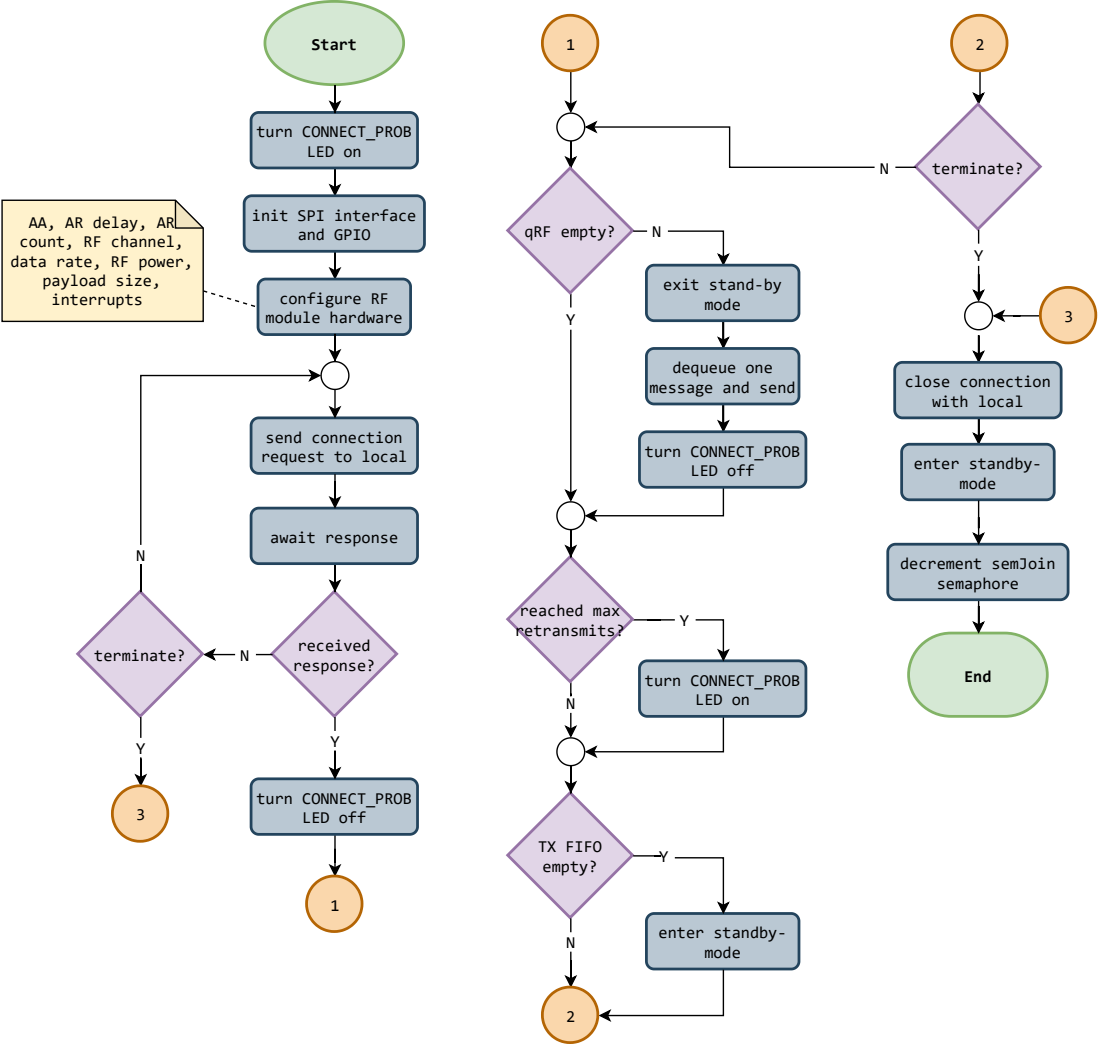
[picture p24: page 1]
Start; configure RF module hardware; turn CONNECT_PROB LED on; received response?; await response; turn CONNECT_PROB LED off; qRF empty?; TX FIFO empty?; reached max retransmits?; enter standby- mode; End; terminate?; close connection with local; decrement semJoin semaphore

init SPI interface
and GPIO

AA, AR delay, AR
count, RF channel,
data rate, RF power,
payload size,
interrupts

exit stand-by
mode

dequeue one
message and send

send connection
request to local

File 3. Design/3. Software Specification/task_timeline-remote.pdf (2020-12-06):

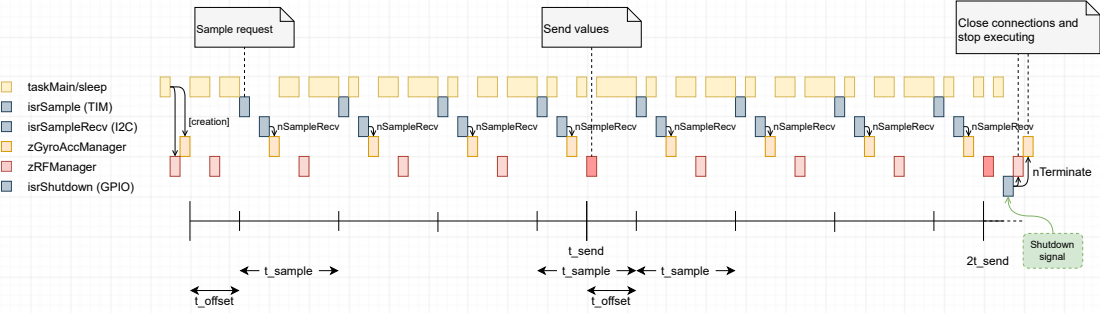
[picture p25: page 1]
taskMain/sleep; zGyroAccManager; nSampleRecv; t_send; 2t_send; t_offset; t_sample; zRFManager; Sample request; isrShutdown (GPIO); nTerminate; nSampleRecv [creation]; Send values; Shutdown signal; isrSample (TIM); isrSampleRecv (I2C)

Close connections and
stop executing

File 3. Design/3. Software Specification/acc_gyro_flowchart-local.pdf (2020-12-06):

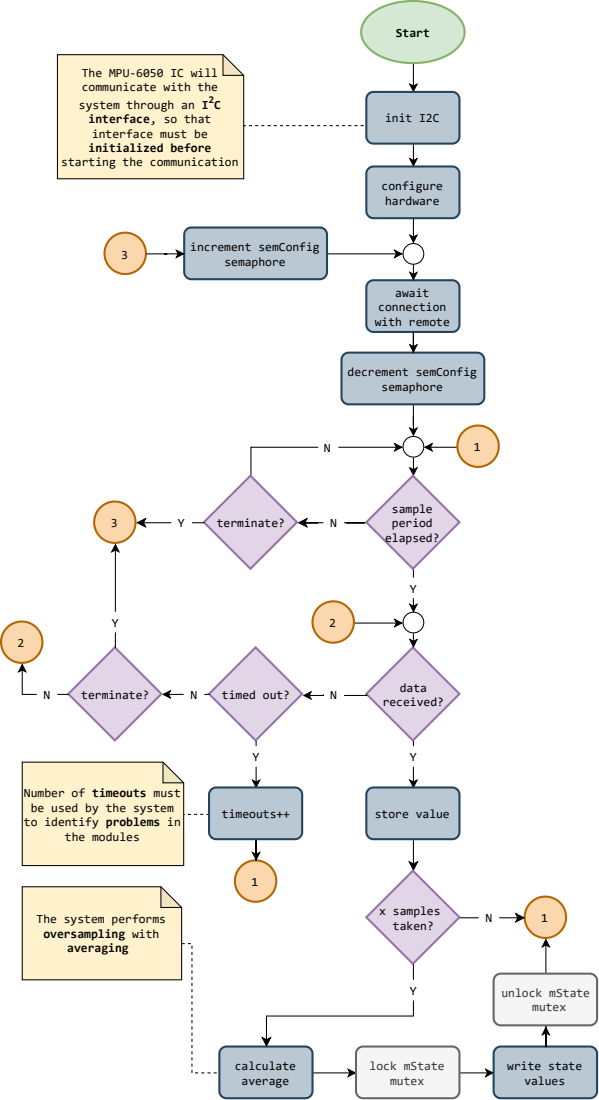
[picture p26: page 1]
Start; data received?; timed out?; sample period elapsed?; terminate?; init I2C; configure hardware; timeouts++; store value; calculate average; x samples taken?; lock mState mutex; write state values; unlock mState mutex; await connection with remote; decrement semConfig semaphore; increment semConfig semaphore

The MPU-6050 IC will
communicate with the
system through an I
interface, so that
interface must be
initialized before
starting the communication

Number of timeouts must
be used by the system
to identify problems in
the modules

The system performs
oversampling with
averaging

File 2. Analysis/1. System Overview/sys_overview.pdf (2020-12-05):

## Zephyrus

Main Board | Remote Board

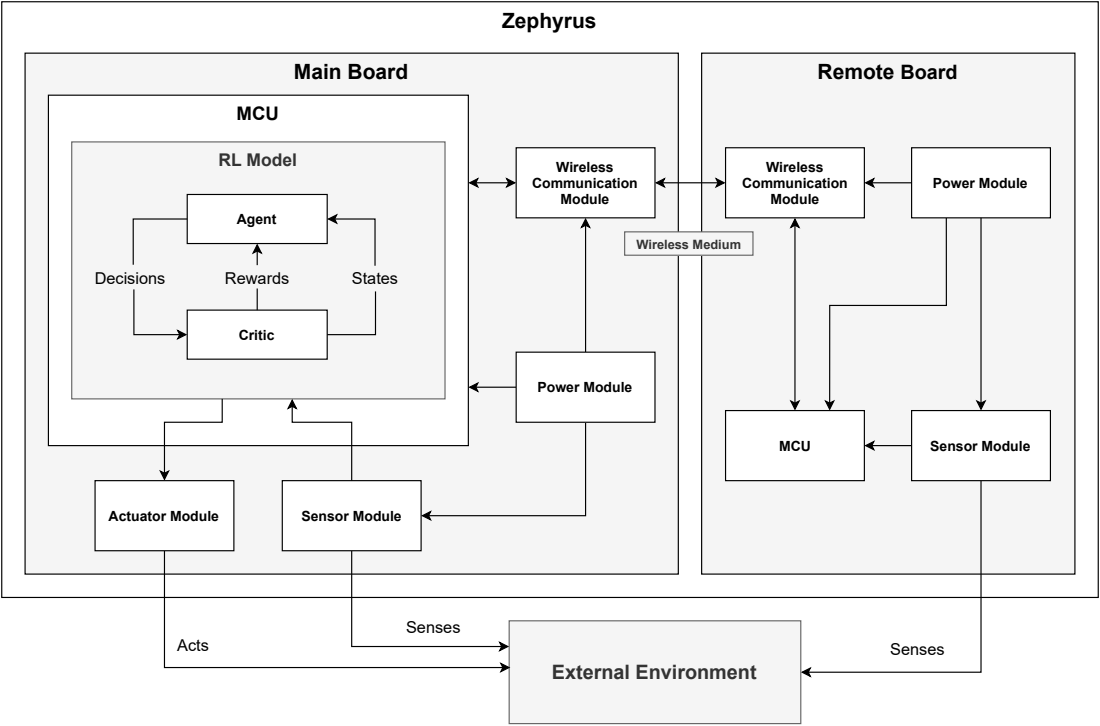
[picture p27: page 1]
MCU; RL Model; Wireless Medium; External Environment; Senses; Critic; Agent; Acts; Decisions; Rewards; States; Actuator Module; Wireless Communication Module; Power Module; Sensor Module

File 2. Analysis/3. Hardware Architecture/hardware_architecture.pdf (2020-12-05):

### External Environment

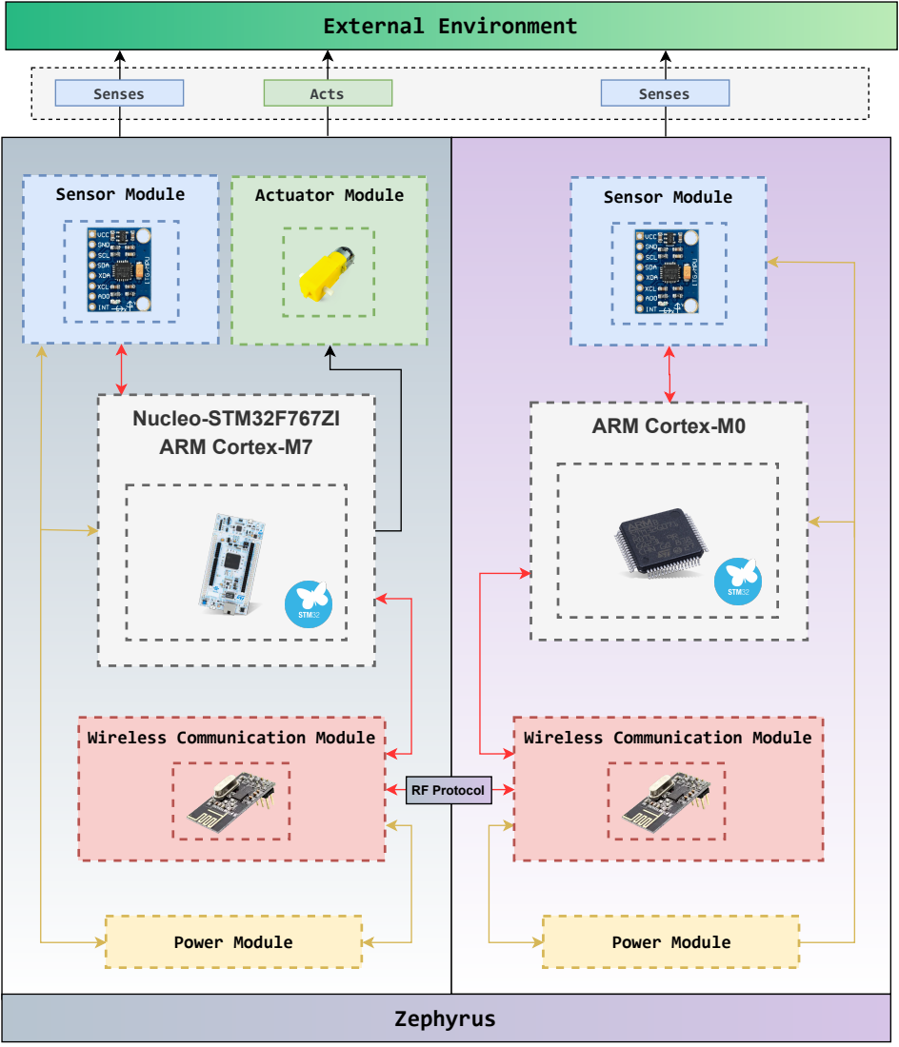
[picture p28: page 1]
Sensor Module; Nucleo-STM32F767ZI ARM Cortex-M7; Zephyrus; ARM Cortex-M0; Power Module; Actuator Module; RF Protocol; Senses; Acts

Wireless Communication Module

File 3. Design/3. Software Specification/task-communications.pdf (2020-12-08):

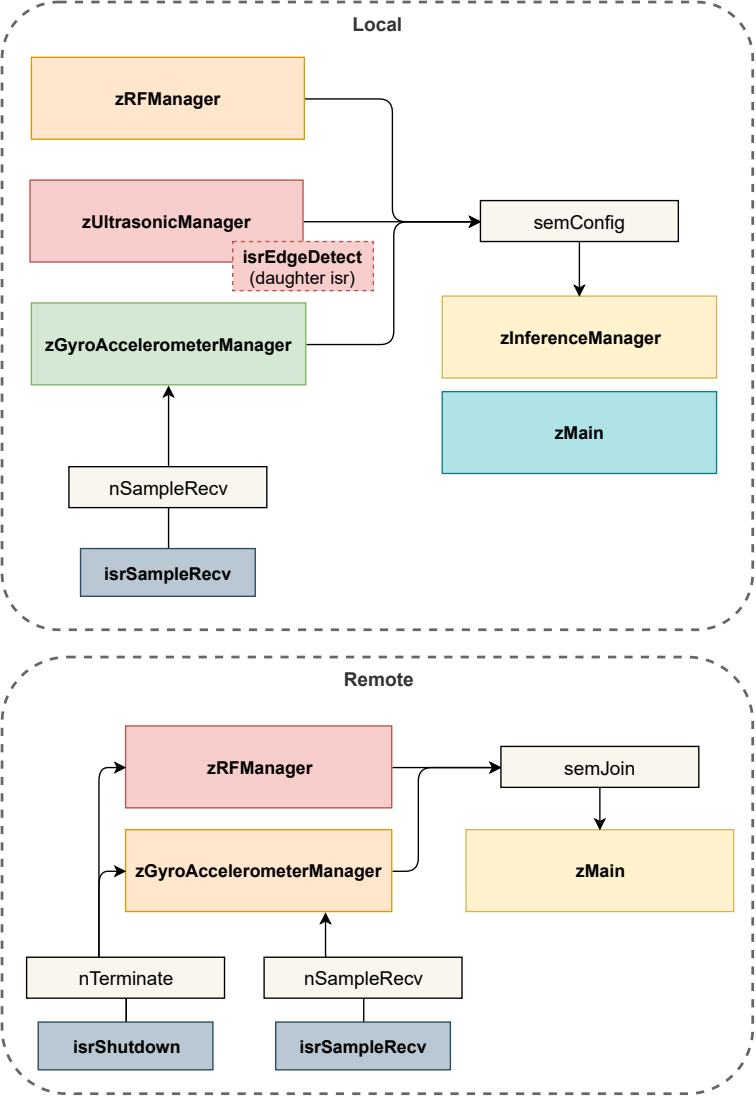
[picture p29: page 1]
Remote; Local; zUltrasonicManager; zGyroAccelerometerManager; isrEdgeDetect (daughter isr); zMain; zRFManager; zInferenceManager; semConfig; isrSampleRecv; nSampleRecv; semJoin; isrShutdown; nTerminate

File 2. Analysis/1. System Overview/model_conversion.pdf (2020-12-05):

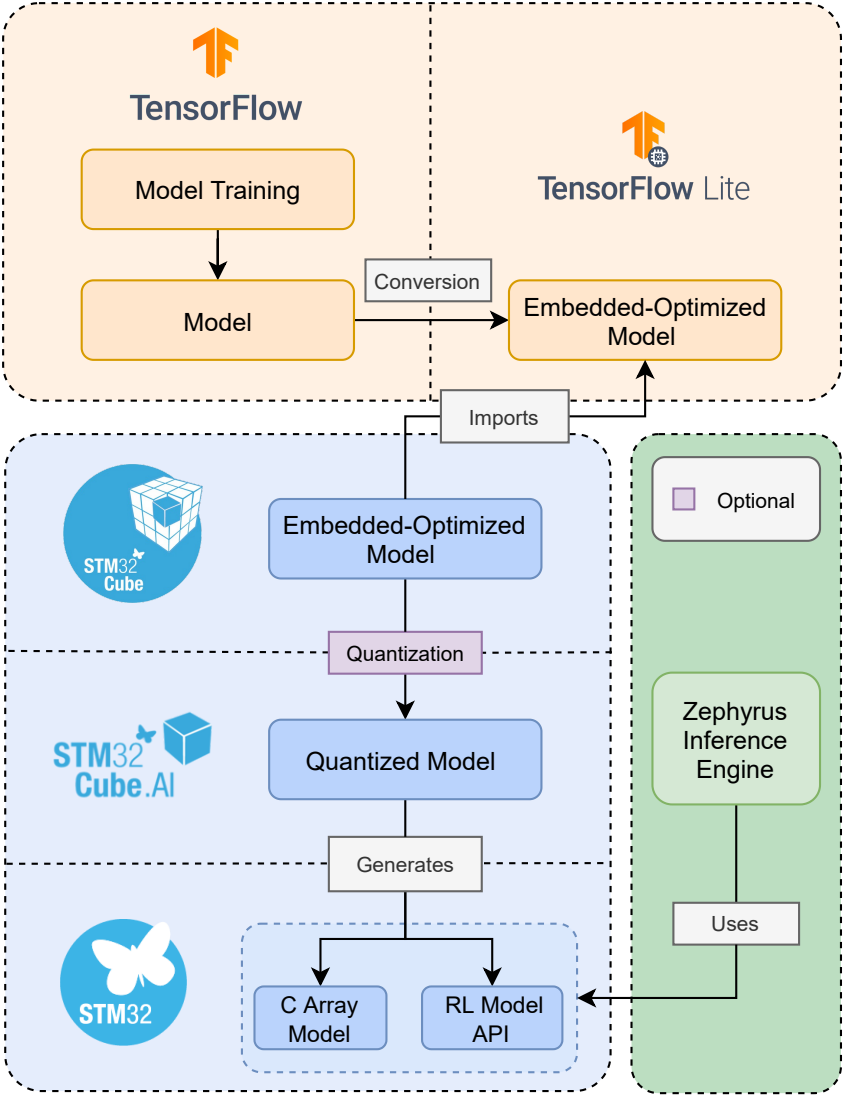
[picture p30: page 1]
Model Training; Quantization; Generates; Model; Embedded-Optimized; Embedded-Optimized Model; Quantized Model; RL Model API; C Array Model; Zephyrus Inference Engine; Uses; Conversion; Imports; Optional

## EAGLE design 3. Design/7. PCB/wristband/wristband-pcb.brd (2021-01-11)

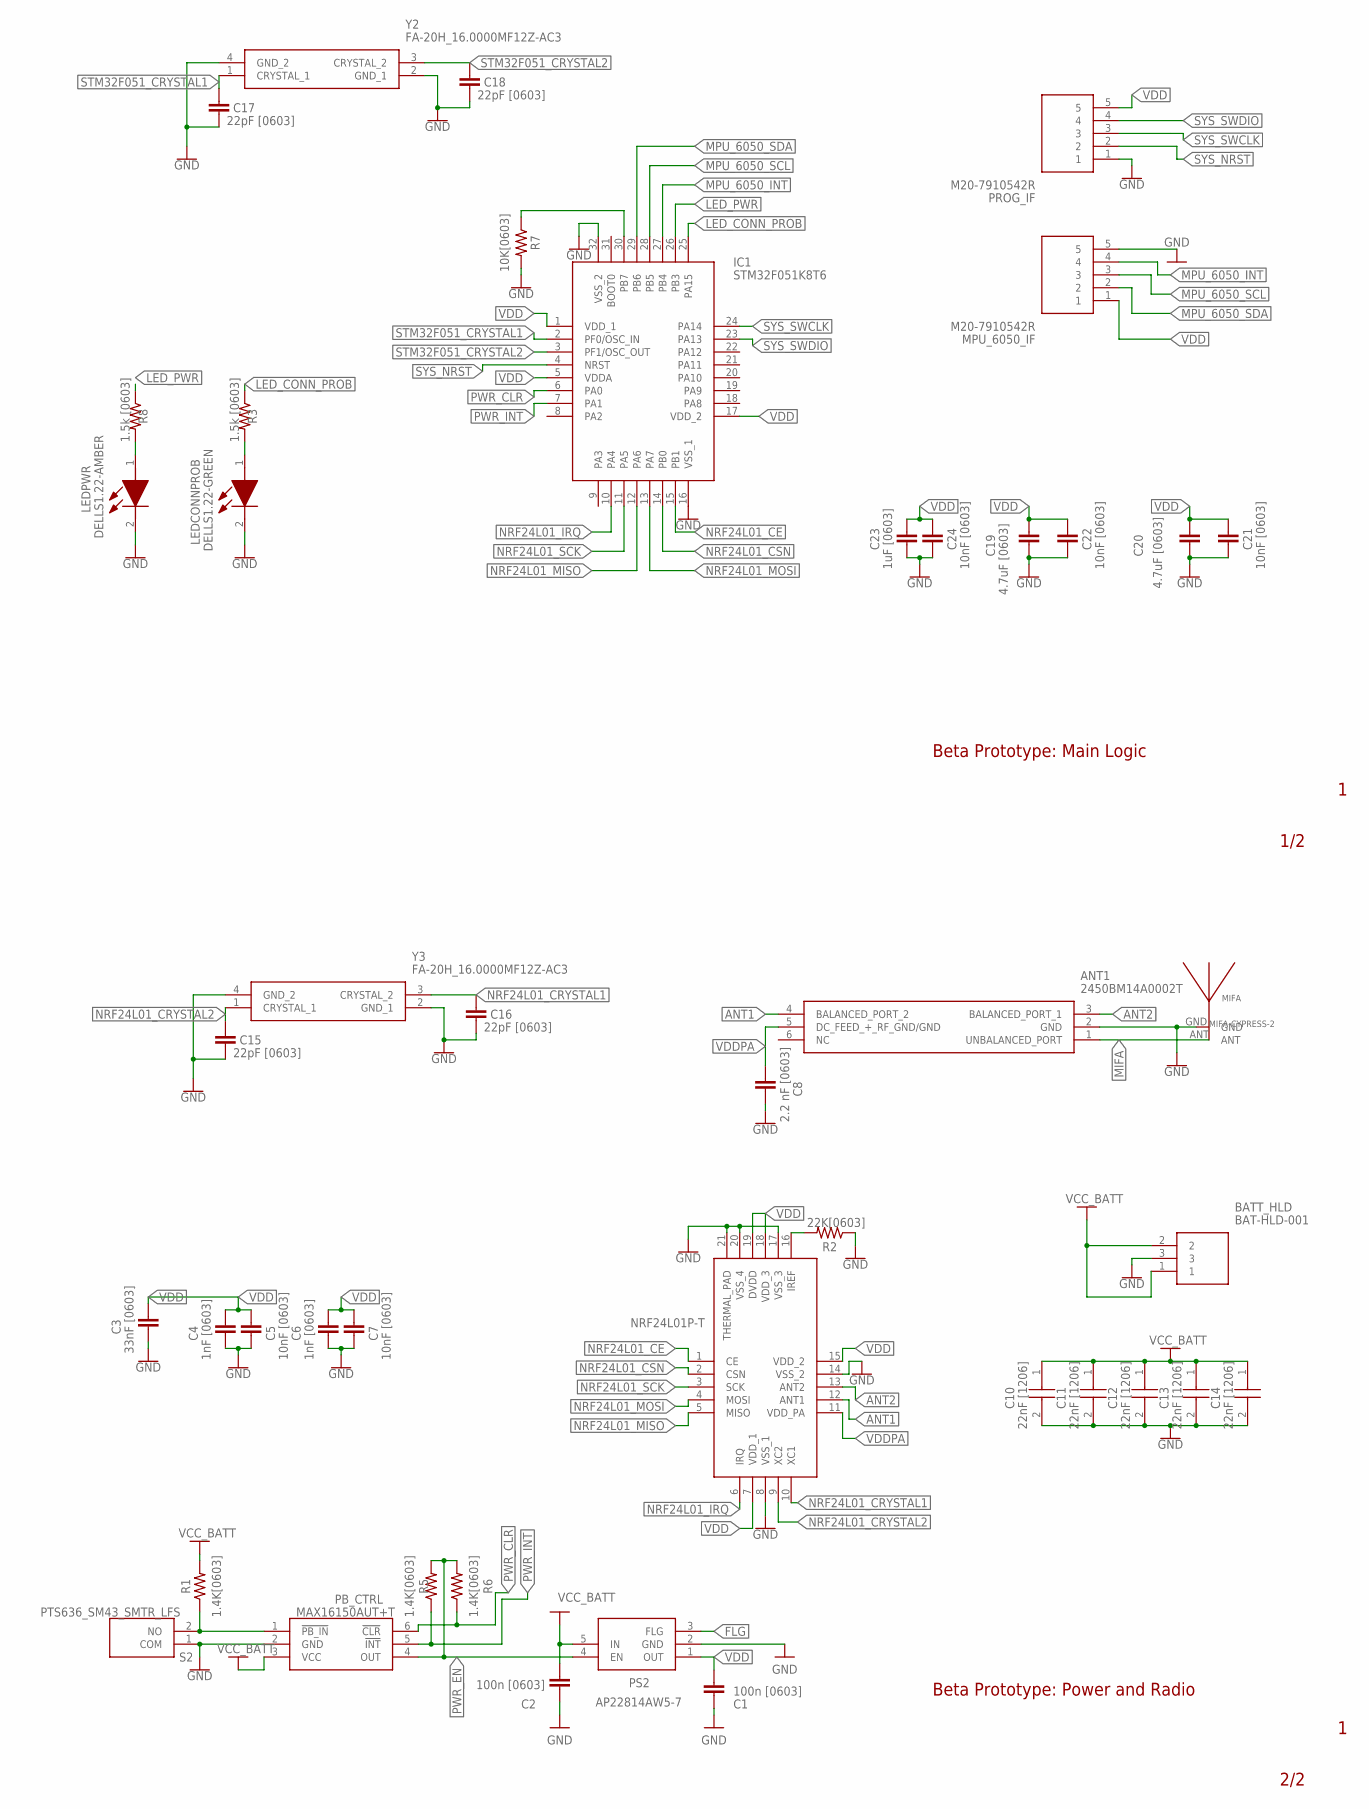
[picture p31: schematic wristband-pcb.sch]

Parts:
ANT1: 2450BM14A0002T
BATT_HLD: BAT-HLD-001; BATHLD001
C1, C2: 100n [0603]; CAPC1608X85
C3: 33nF [0603]; RESC0603_L
C4, C6: 1nF [0603]; RESC0603_L
C5, C7, C21, C22, C24: 10nF [0603]; RESC0603_L
C8: 2.2 nF [0603]; RESC0603_L
C10, C11, C12, C13, C14: 22nF [1206]; CAPC3216X180N
C15, C16, C17, C18: 22pF [0603]; RESC0603_L
C19, C20: 4.7uF [0603]; RESC0603_L
C23: 1uF [0603]; RESC0603_L
IC1: STM32F051K8T6; QFP80P900X900X160-32N
LEDCONNPROB: DELLS1.22-GREEN; KSDELLS122JHKI1
LEDPWR: DELLS1.22-AMBER; KSDELLS122JHKI1
MIFA: MIFA-CYPRESS-2
MPU_6050_IF: M20-7910542R; M207910542R
NRF24L01+: NRF24L01P-T; QFN50P400X400X95-21N
PB_CTRL: MAX16150AUT+T; SOT95P280X145-6N
PROG_IF: M20-7910542R; M207910542R
PS2: AP22814AW5-7; SOT95P285X130-5N
R1, R5, R6: 1.4K[0603]; RESC1608X60
R2: 22K[0603]; RESC1608X60
R3, R8: 1.5k [0603]; RESC1608X60
R7: 10K[0603]; RESC1608X60
S2: PTS636_SM43_SMTR_LFS; PTS636SM43SMTRLFS
Y2, Y3: FA-20H_16.0000MF12Z-AC3; FA20H160000MF12ZAC3

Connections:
ANT1: ANT1.4 (BALANCED_PORT_2), NRF24L01+.12 (ANT1)
ANT2: ANT1.3 (BALANCED_PORT_1), NRF24L01+.13 (ANT2)
FLG: PS2.3 (FLG)
GND: ANT1.2 (GND), BATT_HLD.3, C1.2, C2.2, C3.2, C4.2, C5.2, C6.2, C7.2, C8.2, C10.2, C11.2, C12.2, C13.2, C14.2, C15.2, C16.2, C17.2, C18.2, C19.2, C20.2, C21.2, C22.2, C23.2, C24.2, IC1.16 (VSS_1), IC1.32 (VSS_2), LEDCONNPROB.2 (K), LEDPWR.2 (K), MIFA.GND, MPU_6050_IF.5, NRF24L01+.8 (VSS_1), NRF24L01+.14 (VSS_2), NRF24L01+.17 (VSS_3), NRF24L01+.20 (VSS_4), NRF24L01+.21 (THERMAL_PAD), PB_CTRL.2 (GND), PROG_IF.1, PS2.2 (GND), R2.1, R7.2, S2.1 (COM), Y2.2 (GND_1), Y2.4 (GND_2), Y3.2 (GND_1), Y3.4 (GND_2)
LED_CONN_PROB: IC1.25 (PA15), R3.1
LED_PWR: IC1.26 (PB3), R8.1
MIFA: ANT1.1 (UNBALANCED_PORT), MIFA.ANT
MPU_6050_INT: IC1.27 (PB4), MPU_6050_IF.4
MPU_6050_SCL: IC1.28 (PB5), MPU_6050_IF.3
MPU_6050_SDA: IC1.29 (PB6), MPU_6050_IF.2
unnamed: PB_CTRL.1 (!PB_IN), R1.1, S2.2 (NO)
unnamed: NRF24L01+.16 (IREF), R2.2
unnamed: IC1.30 (PB7), R7.1
unnamed: LEDPWR.1 (A), R8.2
unnamed: LEDCONNPROB.1 (A), R3.2
NRF24L01_CE: IC1.15 (PB1), NRF24L01+.1 (CE)
NRF24L01_CRYSTAL1: C16.1, NRF24L01+.10 (XC1), Y3.3 (CRYSTAL_2)
NRF24L01_CRYSTAL2: C15.1, NRF24L01+.9 (XC2), Y3.1 (CRYSTAL_1)
NRF24L01_CSN: IC1.14 (PB0), NRF24L01+.2 (CSN)
NRF24L01_IRQ: IC1.10 (PA4), NRF24L01+.6 (IRQ)
NRF24L01_MISO: IC1.12 (PA6), NRF24L01+.5 (MISO)
NRF24L01_MOSI: IC1.13 (PA7), NRF24L01+.4 (MOSI)
NRF24L01_SCK: IC1.11 (PA5), NRF24L01+.3 (SCK)
PWR_CLR: IC1.6 (PA0), PB_CTRL.6 (!CLR), R6.1
PWR_EN: PB_CTRL.4 (OUT), PS2.4 (EN), R5.2, R6.2
PWR_INT: IC1.7 (PA1), PB_CTRL.5 (!INT), R5.1
STM32F051_CRYSTAL1: C17.1, IC1.2 (PF0/OSC_IN), Y2.1 (CRYSTAL_1)
STM32F051_CRYSTAL2: C18.1, IC1.3 (PF1/OSC_OUT), Y2.3 (CRYSTAL_2)
SYS_NRST: IC1.4 (NRST), PROG_IF.2
SYS_SWCLK: IC1.24 (PA14), PROG_IF.3
SYS_SWDIO: IC1.23 (PA13), PROG_IF.4
VCC_BATT: BATT_HLD.1, BATT_HLD.2, C2.1, C10.1, C11.1, C12.1, C13.1, C14.1, PB_CTRL.3 (VCC), PS2.5 (IN), R1.2
VDD: C1.1, C3.1, C4.1, C5.1, C6.1, C7.1, C19.1, C20.1, C21.1, C22.1, C23.1, C24.1, IC1.1 (VDD_1), IC1.5 (VDDA), IC1.17 (VDD_2), MPU_6050_IF.1, NRF24L01+.7 (VDD_1), NRF24L01+.15 (VDD_2), NRF24L01+.18 (VDD_3), NRF24L01+.19 (DVDD), PROG_IF.5, PS2.1 (OUT)
VDDPA: ANT1.5 (DC_FEED_+_RF_GND/GND), C8.1, NRF24L01+.11 (VDD_PA)

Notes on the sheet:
1/2
2/2
Beta Prototype: Main Logic
Beta Prototype: Power and Radio

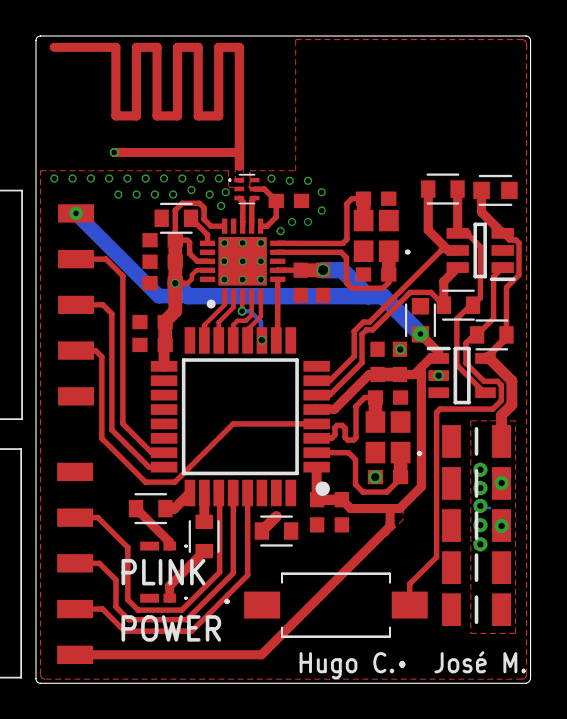
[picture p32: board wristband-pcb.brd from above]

Board: 2 copper layers, 27.5 x 36.0 mm, 44 parts (1 on the bottom side), 33 nets.

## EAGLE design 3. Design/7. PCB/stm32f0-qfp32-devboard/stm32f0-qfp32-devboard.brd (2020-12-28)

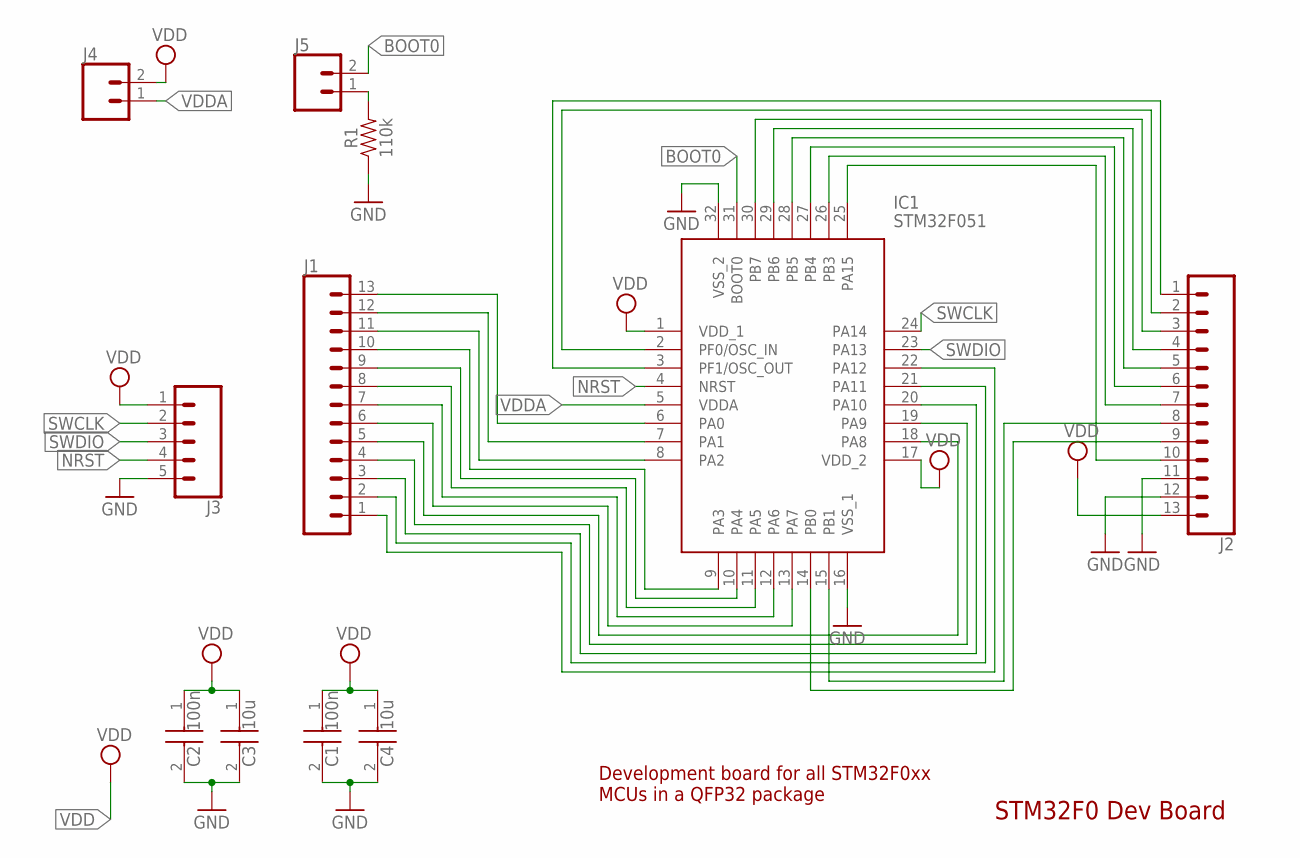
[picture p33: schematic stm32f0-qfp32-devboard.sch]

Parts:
C1, C2: 100n; CAPC2012X100N
C3, C4: 10u; CAPC3216X180N
IC1: STM32F051; QFP80P900X900X160-32N
J1, J2: CONN_13; 1X13
J3: CONN_05; 1X05
J4, J5: CONN_02; 1X02
R1: 110k; 0805

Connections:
BOOT0: IC1.31 (BOOT0), J5.2
GND: C1.2, C2.2, C3.2, C4.2, IC1.16 (VSS_1), IC1.32 (VSS_2), J2.11, J2.12, J3.5, R1.1
unnamed: IC1.6 (PA0), J1.13
unnamed: IC1.7 (PA1), J1.12
unnamed: IC1.2 (PF0/OSC_IN), J2.2
unnamed: IC1.3 (PF1/OSC_OUT), J2.1
unnamed: IC1.30 (PB7), J2.3
unnamed: IC1.29 (PB6), J2.4
unnamed: IC1.28 (PB5), J2.5
unnamed: IC1.27 (PB4), J2.6
unnamed: IC1.26 (PB3), J2.7
unnamed: IC1.15 (PB1), J2.8
unnamed: IC1.14 (PB0), J2.9
unnamed: IC1.8 (PA2), J1.11
unnamed: IC1.9 (PA3), J1.10
unnamed: IC1.10 (PA4), J1.9
unnamed: IC1.11 (PA5), J1.8
unnamed: IC1.12 (PA6), J1.7
unnamed: IC1.13 (PA7), J1.6
unnamed: IC1.18 (PA8), J1.5
unnamed: IC1.19 (PA9), J1.4
unnamed: IC1.20 (PA10), J1.3
unnamed: IC1.21 (PA11), J1.2
unnamed: IC1.22 (PA12), J1.1
unnamed: IC1.25 (PA15), J2.10
unnamed: J5.1, R1.2
NRST: IC1.4 (NRST), J3.4
SWCLK: IC1.24 (PA14), J3.2
SWDIO: IC1.23 (PA13), J3.3
VDD: C1.1, C2.1, C3.1, C4.1, IC1.1 (VDD_1), IC1.17 (VDD_2), J2.13, J3.1, J4.2
VDDA: IC1.5 (VDDA), J4.1

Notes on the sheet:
STM32F0 Dev Board
Development board for all STM32F0xx MCUs in a QFP32 package

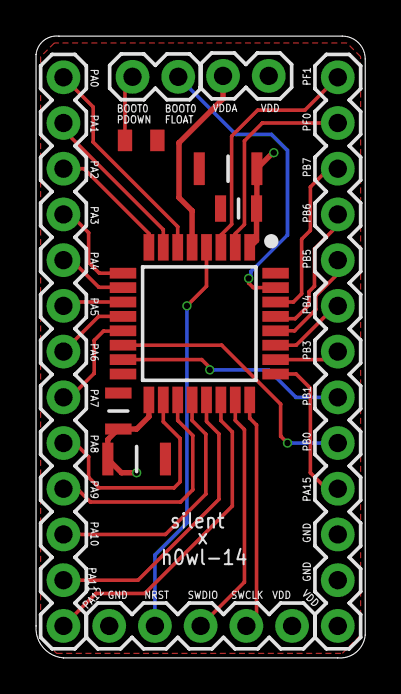
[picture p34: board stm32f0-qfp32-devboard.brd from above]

Board: 2 copper layers, 18.3 x 34.6 mm, 11 parts (0 on the bottom side), 31 nets.

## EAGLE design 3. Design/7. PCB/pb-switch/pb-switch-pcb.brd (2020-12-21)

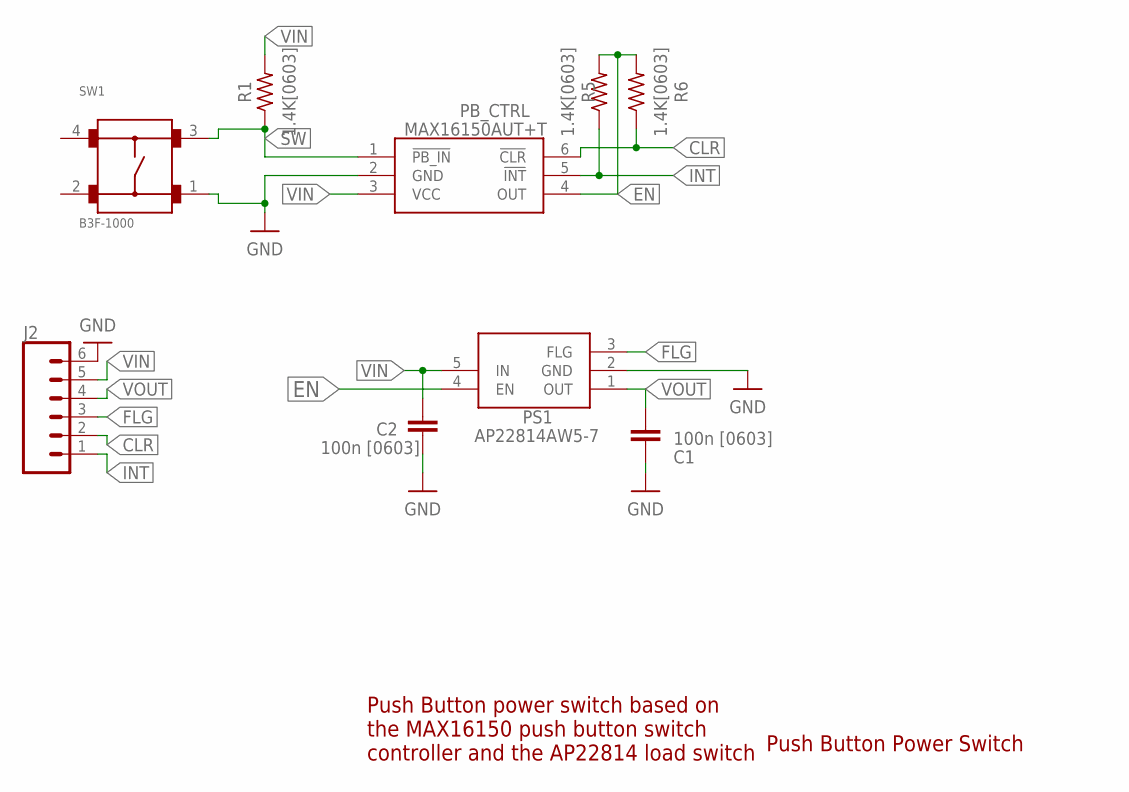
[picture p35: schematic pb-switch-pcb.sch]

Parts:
C1, C2: 100n [0603]; CAPC1608X85
J2: CONN_06SILK_FEMALE_PTH; 1X06
PB_CTRL: MAX16150AUT+T; SOT95P280X145-6N
PS1: AP22814AW5-7; SOT95P285X130-5N
R1, R5, R6: 1.4K[0603]; RESC1608X60
SW1: B3F-1000

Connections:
CLR: J2.2, PB_CTRL.6 (!CLR), R6.1
EN: PB_CTRL.4 (OUT), PS1.4 (EN), R5.2, R6.2
FLG: J2.3, PS1.3 (FLG)
GND: C1.2, C2.2, J2.6, PB_CTRL.2 (GND), PS1.2 (GND), SW1.1
INT: J2.1, PB_CTRL.5 (!INT), R5.1
SW: PB_CTRL.1 (!PB_IN), R1.1, SW1.3
VIN: C2.1, J2.5, PB_CTRL.3 (VCC), PS1.5 (IN), R1.2
VOUT: C1.1, J2.4, PS1.1 (OUT)

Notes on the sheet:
Push Button Power Switch
Push Button power switch based on the MAX16150 push button switch controller and the AP22814 load switch

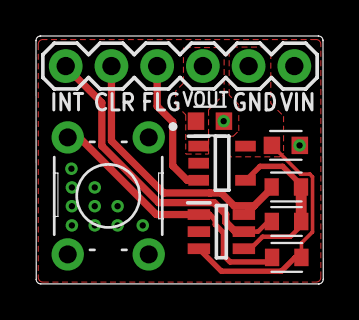
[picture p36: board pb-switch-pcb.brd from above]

Board: 2 copper layers, 16.0 x 13.8 mm, 9 parts (0 on the bottom side), 8 nets.

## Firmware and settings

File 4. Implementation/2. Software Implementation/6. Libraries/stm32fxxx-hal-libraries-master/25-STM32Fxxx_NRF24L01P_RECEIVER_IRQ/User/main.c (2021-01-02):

/**
 * Keil project example for NRF24L01+ using interrupts
 *
 * Receiver code
 *
 * Before you start, select your target, on the right of the "Load" button
 *
 * @author    Tilen MAJERLE
 * @email     tilen@majerle.eu
 * @website   http://stm32f4-discovery.net
 * @ide       Keil uVision 5
 * @conf      PLL parameters are set in "Options for Target" -> "C/C++" -> "Defines"
 * @packs     STM32F4xx/STM32F7xx Keil packs are requred with HAL driver support
 * @stdperiph STM32F4xx/STM32F7xx HAL drivers required
 */
/* Include core modules */
#include "stm32fxxx_hal.h"
/* Include my libraries here */
#include "defines.h"
//#include "tm_stm32_disco.h"
#include "tm_stm32_delay.h"
#include "tm_stm32_nrf24l01.h"
#include "tm_stm32_usart.h"
#include "tm_stm32_exti.h"

/* Receiver address */
uint8_t TxAddress[] = {
	0xE7,
	0xE7,
	0xE7,
	0xE7,
	0xE7
};
/* My address */
uint8_t MyAddress[] = {
	0x7E,
	0x7E,
	0x7E,
	0x7E,
	0x7E
};

/* Data received and data for send */
uint8_t dataIn[32];

/* Interrupt pin settings */
#define IRQ_PORT    GPIOA
#define IRQ_PIN     GPIO_PIN_4

/* NRF transmission status */
TM_NRF24L01_Transmit_Status_t transmissionStatus;
TM_NRF24L01_IRQ_t NRF_IRQ;

int main(void) {
	/* Init system clock for maximum system speed */
	TM_RCC_InitSystem();
	
	/* Init HAL layer */
	HAL_Init();
	
	/* Init leds */
	//TM_DISCO_LedInit();
	
	/* Init button */
	//TM_DISCO_ButtonInit();
	
	/* Initialize USART, TX: PB6, RX: PB7 */
	TM_USART_Init(USART1, TM_USART_PinsPack_2, 115200);
	
	/* Initialize NRF24L01+ on channel 15 and 32bytes of payload */
	/* By default 2Mbps data rate and 0dBm output power */
	/* NRF24L01 goes to RX mode by default */
	TM_NRF24L01_Init(15, 32);
	
	/* Set RF settings, Data rate to 2Mbps, Output power to 0dBm */
	TM_NRF24L01_SetRF(TM_NRF24L01_DataRate_2M, TM_NRF24L01_OutputPower_0dBm);
	
	/* Set my address, 5 bytes */
	TM_NRF24L01_SetMyAddress(MyAddress);
	
	/* Set TX address, 5 bytes */
	TM_NRF24L01_SetTxAddress(TxAddress);
	
	/* Enable interrupts for NRF24L01+ IRQ pin */
	TM_EXTI_Attach(IRQ_PORT, IRQ_PIN, TM_EXTI_Trigger_Falling);

	while (1) {

	}
}

/* Interrupt handler */
void TM_EXTI_Handler(uint16_t GPIO_Pin) {
	/* Check for proper interrupt pin */
	if (GPIO_Pin == IRQ_PIN) {
		/* Read interrupts */
		TM_NRF24L01_Read_Interrupts(&NRF_IRQ);
		
		/* If data is ready on NRF24L01+ */
		if (NRF_IRQ.F.DataReady) {
			/* Get data from NRF24L01+ */
			TM_NRF24L01_GetData(dataIn);
			
			/* Start send */
			//TM_DISCO_LedOn(LED_GREEN);
			
			/* Send it back, NRF goes automatically to TX mode */
			TM_NRF24L01_Transmit(dataIn);
			
			/* Wait for data to be sent */
			do {
				/* Wait till sending */
				transmissionStatus = TM_NRF24L01_GetTransmissionStatus();
			} while (transmissionStatus == TM_NRF24L01_Transmit_Status_Sending);
			
			/* Send done */
			//TM_DISCO_LedOff(LED_GREEN);
			
			/* Go back to RX mode */
			TM_NRF24L01_PowerUpRx();		
		}
		
		/* Clear interrupts */
		TM_NRF24L01_Clear_Interrupts();
	}
}

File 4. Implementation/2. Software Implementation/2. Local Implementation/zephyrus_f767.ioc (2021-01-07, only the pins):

Mcu.UserName=STM32F767ZITx
PA13.Signal=SYS_JTMS-SWDIO
PA14.Signal=SYS_JTCK-SWCLK
PA4.GPIO_Label=BATTERY_LEVEL
PA4.Signal=ADCx_IN4
PB0.GPIO_Label=LED_CONNECT
PB0.Signal=GPIO_Output
PB10.GPIO_Label=USS_ECHO_FRONT
PB10.Signal=S_TIM2_CH3
PB11.GPIO_Label=USS_ECHO_BACK
PB11.Signal=S_TIM2_CH4
PB13.GPIO_Label=MOTOR_R_DIR
PB13.Signal=GPIO_Output
PB14.GPIO_Label=LED_DEBUG2
PB14.Signal=GPIO_Output
PB15.GPIO_Label=MOTOR_L_DIR
PB15.Signal=GPIO_Output
PB3.GPIO_Label=USS_TRIGGER
PB3.Signal=S_TIM2_CH2
PB7.GPIO_Label=LED_POWER
PB7.Signal=S_TIM4_CH2
PB8.GPIO_Label=MPU_6050_SCL
PB8.Signal=I2C1_SCL
PB9.GPIO_Label=MPU_6050_SDA
PB9.Signal=I2C1_SDA
PC10.GPIO_Label=NRF24L01_SCK
PC10.Signal=SPI3_SCK
PC11.GPIO_Label=NRF24L01_MISO
PC11.Signal=SPI3_MISO
PC12.GPIO_Label=NRF24L01_MOSI
PC12.Signal=SPI3_MOSI
PC13.GPIO_Label=BUTTON_DEBUG1
PC13.Signal=GPXTI13
PC14/OSC32_IN.Signal=RCC_OSC32_IN
PC15/OSC32_OUT.Signal=RCC_OSC32_OUT
PC6.GPIO_Label=FLAG_DEBUG
PC6.Signal=GPIO_Output
PC8.GPIO_Label=MOTOR_R_PWM
PC8.Signal=S_TIM3_CH3
PC9.GPIO_Label=MOTOR_L_PWM
PC9.Signal=S_TIM3_CH4
PD2.GPIO_Label=NRF24L01_CSN
PD2.Signal=GPIO_Output
PG2.GPIO_Label=NRF24L01_CE
PG2.Signal=GPIO_Output
PG3.GPIO_Label=NRF24L01_INT
PG3.Signal=GPXTI3
PH0/OSC_IN.Signal=RCC_OSC_IN
PH1/OSC_OUT.Signal=RCC_OSC_OUT

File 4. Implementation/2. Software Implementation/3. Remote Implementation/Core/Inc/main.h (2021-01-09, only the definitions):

#define BATTERY_SAMPLE_PERIOD (1000-1)
#define STM32F051_CRYSTAL1_Pin GPIO_PIN_0
#define STM32F051_CRYSTAL1_GPIO_Port GPIOF
#define STM32F051_CRYSTAL2_Pin GPIO_PIN_1
#define STM32F051_CRYSTAL2_GPIO_Port GPIOF
#define PWR_CLR_Pin GPIO_PIN_0
#define PWR_CLR_GPIO_Port GPIOA
#define PWR_INT_Pin GPIO_PIN_1
#define PWR_INT_GPIO_Port GPIOA
#define PWR_INT_EXTI_IRQn EXTI0_1_IRQn
#define NRF24L01_IRQ_Pin GPIO_PIN_4
#define NRF24L01_IRQ_GPIO_Port GPIOA
#define NRF24L01_IRQ_EXTI_IRQn EXTI4_15_IRQn
#define NRF24L01_SCK_Pin GPIO_PIN_5
#define NRF24L01_SCK_GPIO_Port GPIOA
#define NRF24L01_MISO_Pin GPIO_PIN_6
#define NRF24L01_MISO_GPIO_Port GPIOA
#define NRF24L01_MOSI_Pin GPIO_PIN_7
#define NRF24L01_MOSI_GPIO_Port GPIOA
#define NRF24L01_CSN_Pin GPIO_PIN_0
#define NRF24L01_CSN_GPIO_Port GPIOB
#define NRF24L01_CE_Pin GPIO_PIN_1
#define NRF24L01_CE_GPIO_Port GPIOB
#define FLAG_DEBUG_Pin GPIO_PIN_9
#define FLAG_DEBUG_GPIO_Port GPIOA
#define LED_DEBUG_Pin GPIO_PIN_10
#define LED_DEBUG_GPIO_Port GPIOA
#define LED_CONN_PROB_Pin GPIO_PIN_15
#define LED_CONN_PROB_GPIO_Port GPIOA
#define LED_PWR_Pin GPIO_PIN_3
#define LED_PWR_GPIO_Port GPIOB
#define MPU_6050_SDA_BRIDGE_Pin GPIO_PIN_4
#define MPU_6050_SDA_BRIDGE_GPIO_Port GPIOB
#define MPU_6050_INT_Pin GPIO_PIN_5
#define MPU_6050_INT_GPIO_Port GPIOB
#define MPU_6050_INT_EXTI_IRQn EXTI4_15_IRQn
#define MPU_6050_SCL_Pin GPIO_PIN_6
#define MPU_6050_SCL_GPIO_Port GPIOB
#define MPU_6050_SDA_Pin GPIO_PIN_7
#define MPU_6050_SDA_GPIO_Port GPIOB

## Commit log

2020-10-23 UPTD: Simplified and generalized the wireless connection blocks in the System Overview diragram
2020-10-27 UPDT: Small functional changes to the schematics
2020-10-27 ADD: Sensor frameworks added to the local system's Software Overview
2020-10-31 ADD: Use Case Diagrams
2020-11-01 UPDT: Aesthetic changes to use case diagrams
2020-11-02 FIX: Corrections made to the Use Case diagrams
2020-11-03 ADD: Deliverables section and Shopping List
    [Shopping List.xlsx]
2020-11-04 ADD/UPDT: Material acquisition documentation
    [Shopping List.xlsx]
2020-11-05 UPDT: Use Case Diagram Tweaks
2020-11-06 FIX: Use Case Diagrams
2020-11-06 ADD/UPDT: Updated shopping list with the last purchase
    [Shopping List.xlsx, Zephyrus Shopping List.xlsx]
2020-11-11 FIX: Use case diagram local - added arrow
2020-11-16 FIx: Image tweaks for PowerPoint
2020-11-21 ADD: STM32F051 dev board schematic and PCB
    [copper_bottom.gbr, copper_top.gbr, drill_1_16.xln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]
2020-11-21 ADD: STM32F051 dev board schematic and pcb snapshots
    [stm32f0-qfp32-devboard.brd, stm32f0-qfp32-devboard.sch]
2020-11-22 ADD: Gyroscope & Accelerometer Flowchart + Odel conversion diagram tweak
2020-11-22 ADD: Gyroscope & Accelerometer Flowchart + Model conv. diagram tweaks
2020-11-22 UPDT: Finished gyroscope module's flowchart
2020-11-22 ADD: MPU-6050 interrupt table
2020-11-22 ADD: Images, CAD models and datasheets relative to the Hardware Overview
2020-11-23 ADD: STM32F051 dev board PCB list entry and invoice
    [Zephyrus Shopping List.xlsx]
2020-11-23 FIX: Corrections to the Gyroscope flowchart in the Software Specifications
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2020-11-24 UPDT: Visual Tweaks to the flowcharts and timeline
2020-11-27 ADD: SPI protocol images
2020-11-27 ADD: STM32F0 dev board 3D model
    [C2012X7R1H104K085AA.stp, C3216X7R1C106K160AC.stp, CRCW0805100KFKEA.stp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]
2020-11-29 ADD: Boilerplate material for the wristband PCB
    [C2012X7R1H104K085AA.stp, C3216X7R1C106K160AC.stp, CRCW0805100KFKEA.stp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]
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2020-12-03 UPDT: Waterfall schematic to PDF
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2020-12-05 ADD: Power supply overview pdf export
2020-12-05 ADD|UPDT: Added new antenna library files and initial nRF24L01-balun/filter-antenna interaction sketch
    [2450BM14A0002T.stp, wristband.brd, wristband.sch]
2020-12-05 ADD: acc and gyro task local
2020-12-05 ADD: acc and gyro task remote
2020-12-05 ADD: created drawios for uss and motor flowcharts
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2020-12-05 FIX: Fixed STM32F0 devboard dimensions schematic
2020-12-05 UPDT: RF management thread flowchart
2020-12-05 UPDT: General flowchart and export update
2020-12-06 FIX: minor fix - acc and gyro flowchart
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2020-12-06 ADD|UPDT|FIX: Added last task flowcharts, deleted/corrected unnecessary ones and corrected exports
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2020-12-08 ADD|UPDT|FIX: Corrected Dev Board exports and finished wristband board's schematic
    [2N7002NXAKR.stp, BAT-HLD-001.stp, C2012X7R1H104K085AA.stp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]
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2020-12-10 ADD|UPDT: Finished presentation
    [wristband-pcb.brd]
2020-12-14 UPDT: Added all work done on the Wristband PCB board so far
    [wristband-pcb.brd, wristband-pcb.sch]
2020-12-14 ADD: PB switch PCB
    [2N7002NXAKR.stp, MAX16150AUT+T.stp, pb-switch-pcb.brd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]
2020-12-14 ADD|UPDT: PB switch PCB 3D model
    [pb-switch-pcb.brd, pb-switch-pcb.f3d, pb-switch-pcb.sch]
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2020-12-18 UPDT: PCB Wristband
    [wristband-pcb.brd, wristband-pcb.sch]
2020-12-18 FIX: replaced load switching MOSFET with an actual load switch
    [AP22814AW5-7.stp, pb-switch-pcb.brd, pb-switch-pcb.sch]
2020-12-19 UPDT: Added bypass capacitor at the output, enlarged power paths and optimized power
    [pb-switch-pcb.brd, pb-switch-pcb.sch]
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2020-12-19 UPDT: Added Load Switch to Wristband PCB
    [wristband-pcb.brd, wristband-pcb.sch]
2020-12-20 UPDT: Updated wristband PCB design with new connections and slightly different layout
    [cap_1206.stp, wristband-pcb.brd, wristband-pcb.sch]
2020-12-20 UPDT: Thermal improvements to the pushbutton switch PCB
    [pb-switch-pcb.brd]
2020-12-20 UPDT: Wristband PCB
    [wristband-pcb.brd, wristband-pcb.sch]
2020-12-20 UPDT: Further updates to the wristband PCB
    [wristband-pcb.brd, wristband-pcb.sch]
2020-12-20 UPDT: Functional part of the wristband PCB done
    [wristband-pcb.brd]
2020-12-20 UPDT: Signature overlay added to wristband PCB
    [wristband-pcb.brd]
2020-12-20 UPDT: Almost all 3D models applied in the wristband pcb
    [2N7002NXAKR.stp, CH_DELSS1.22-S1T2-35.stp, PTS636_SM25F_SMTR_LFS.stp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]
2020-12-21 ADD|UPDT: Exported new and corrected old 3D models, 2D models and technical drawings of all PCBs
    [pb-switch-pcb.brd, pb-switch-pcb.f3d, pb-switch-pcb.sch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]
2020-12-21 ADD: pb-switch and stm32f0-qfp32-devboard BOM
    [2N7002NXAKR.stp, AP22814AW5-7.stp, MAX16150AUT+T.stp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]
2020-12-22 ADD: pb-switch and wristband CAM files
    [pb-switch-bom.xlsx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]
2020-12-22 UPDT: Shopping documents
    [Zephyrus Shopping List.xlsx]
2020-12-23 UPDT: Local Implementation - start thread sleep and battery level
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2020-12-23 ADD: Run Mode vs Low Power Modes Simulations
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2020-12-24 UPDT: Battery level assessment dynamic done and tested
2020-12-24 UPDT: Sleep mode added to the main thread
2020-12-26 UPDT: Ported working ultrasonic sensor module from the testing setup to the local system's implementation
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2020-12-27 ADD|UPDT: Added non-tested IMU module and updated thread code and rtos wrapper to use wrapper queueing functions
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2020-12-28 ADD: High-quality rendering of the stm32f0 devboard
    [stm32f0-qfp32-devboard.brd]
2020-12-30 UPDT: Low Battery check routine working on remote system working
    [Zephyrus Shopping List.xlsx]
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2020-12-31 FIX: More reliable startup in debug mode
    [F051qfp_CubeMX.ioc]
2020-12-31 UPDT: TIM3 doing power LED and ADC timing
2020-12-31 UPDT: Added low power mode to MPU module
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2021-01-02 ADD: Preliminary power consumption simulations for the remote system
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2021-01-02 UPDT: Remote task timeline to include only 1 sampling instance and interrupts
2021-01-07 UPDT: Synchronization apparently not working
    [_threads.c, main.c, main.h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]
2021-01-11 Project at the time of delivery
    [Zephyrus Shopping List.xlsx, wristband-pcb.brd, wristband-pcb.sch]

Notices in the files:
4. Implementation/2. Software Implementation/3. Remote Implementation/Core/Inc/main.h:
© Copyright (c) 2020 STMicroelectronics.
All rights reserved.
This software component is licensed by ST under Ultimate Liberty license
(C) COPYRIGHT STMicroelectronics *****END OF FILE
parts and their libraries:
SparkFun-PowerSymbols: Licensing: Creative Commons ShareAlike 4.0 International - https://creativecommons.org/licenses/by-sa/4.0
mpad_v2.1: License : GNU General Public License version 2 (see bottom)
